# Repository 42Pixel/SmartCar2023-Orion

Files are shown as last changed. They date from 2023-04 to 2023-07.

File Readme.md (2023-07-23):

# 第十八届大学生智能汽车竞赛——猎户座

## 仓库简介
&emsp;&emsp;该仓库为第十八届大学生智能汽车竞赛安徽赛区**猎户座**参赛队伍项目仓库，保存了目前猎户座的全部软硬件资料。

## 目录结构
```
└─Fastest-Car
│  └─ProjectFiles
│      ├─Appendix
│      ├─Hardware
│      │  ├─无线串口模块
│      │  └─猎户座
│      │      ├─FastestCar-Motor
│      │      ├─FastestCar_Ctl
│      │      └─Library
│      └─Software
```
**[Appendix](https://github.com/42Pixel/Fastest-Car/tree/main/ProjectFiles/Appendix):** 附件文件夹，存放参考原理图，开源库，图片等相关文件

**[Hardware](https://github.com/42Pixel/Fastest-Car/tree/main/ProjectFiles/Hardware):** 硬件文件夹，存放相关硬件资料:

&emsp;&emsp;<font size=2>[无线串口模块](https://github.com/42Pixel/Fastest-Car/tree/main/ProjectFiles/Hardware/%E6%97%A0%E7%BA%BF%E4%B8%B2%E5%8F%A3%E6%A8%A1%E5%9D%97): 基于433MHZ模块设计的用于智能车急速越野组户外数据透传使用(该项目利用立创EDA设计，请使用立创EDA导入)</font>

&emsp;&emsp;<font size=2>[猎户座](https://github.com/42Pixel/Fastest-Car/tree/main/ProjectFiles/Hardware/%E7%8C%8E%E6%88%B7%E5%BA%A7):  根据开源项目：[逐飞科技基于英飞凌TC264 GTM单元的智能车BLDC开源项目](https://gitee.com/seekfree/TC264_GTM_BLDC_Project.git)修改而成。“[FastestCar-Motor](https://github.com/42Pixel/Fastest-Car/tree/main/ProjectFiles/Hardware/%E7%8C%8E%E6%88%B7%E5%BA%A7/FastestCar-Motor)”为无刷电机驱动部分，“[FastestCar_Ctl](https://github.com/42Pixel/Fastest-Car/tree/main/ProjectFiles/Hardware/%E7%8C%8E%E6%88%B7%E5%BA%A7/FastestCar_Ctl)”为驱动控制部分，“[Library](https://github.com/42Pixel/Fastest-Car/tree/main/ProjectFiles/Hardware/%E7%8C%8E%E6%88%B7%E5%BA%A7/Library)”为元器件封装库</font> 

**[Software](https://github.com/42Pixel/Fastest-Car/tree/main/ProjectFiles/Software):** 软件文件夹，存放程序固件。

## 相关图片

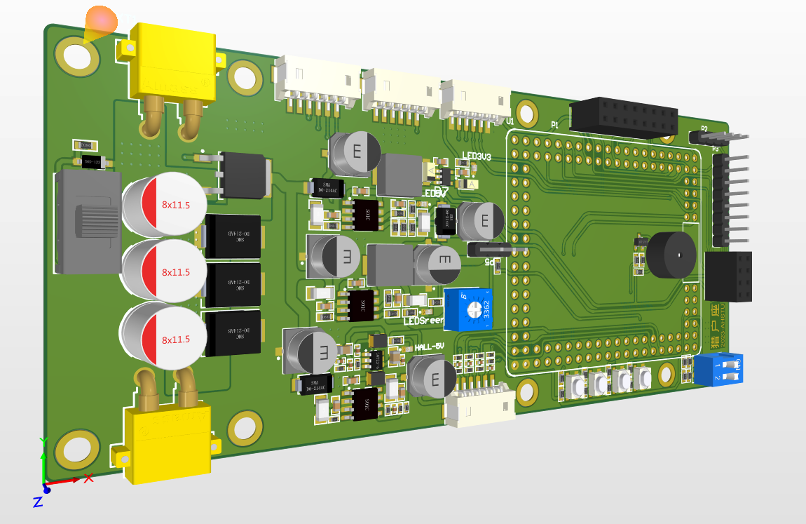
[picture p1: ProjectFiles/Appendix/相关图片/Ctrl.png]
母板

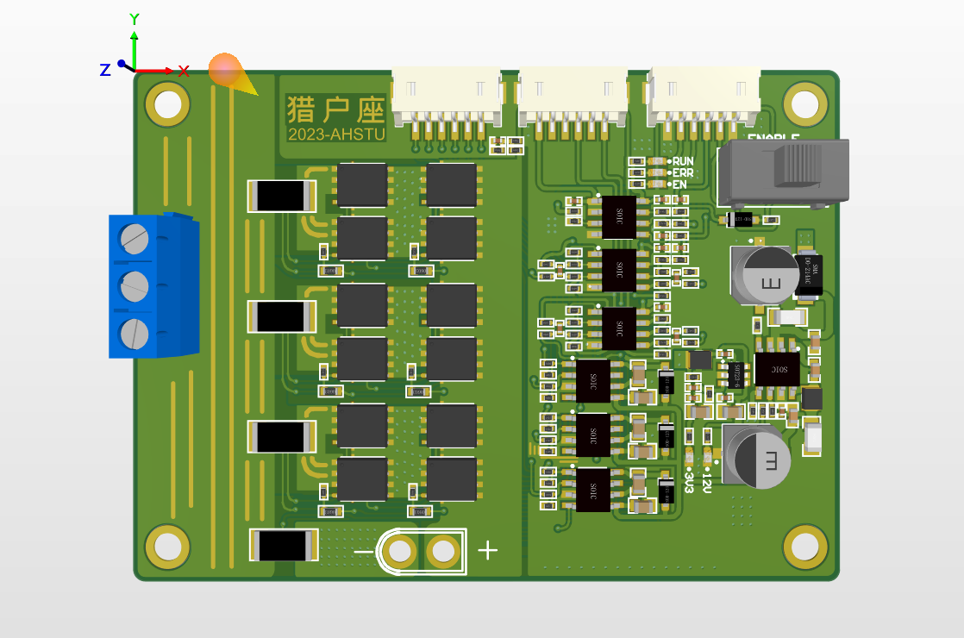
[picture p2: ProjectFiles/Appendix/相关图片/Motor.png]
电机驱动板

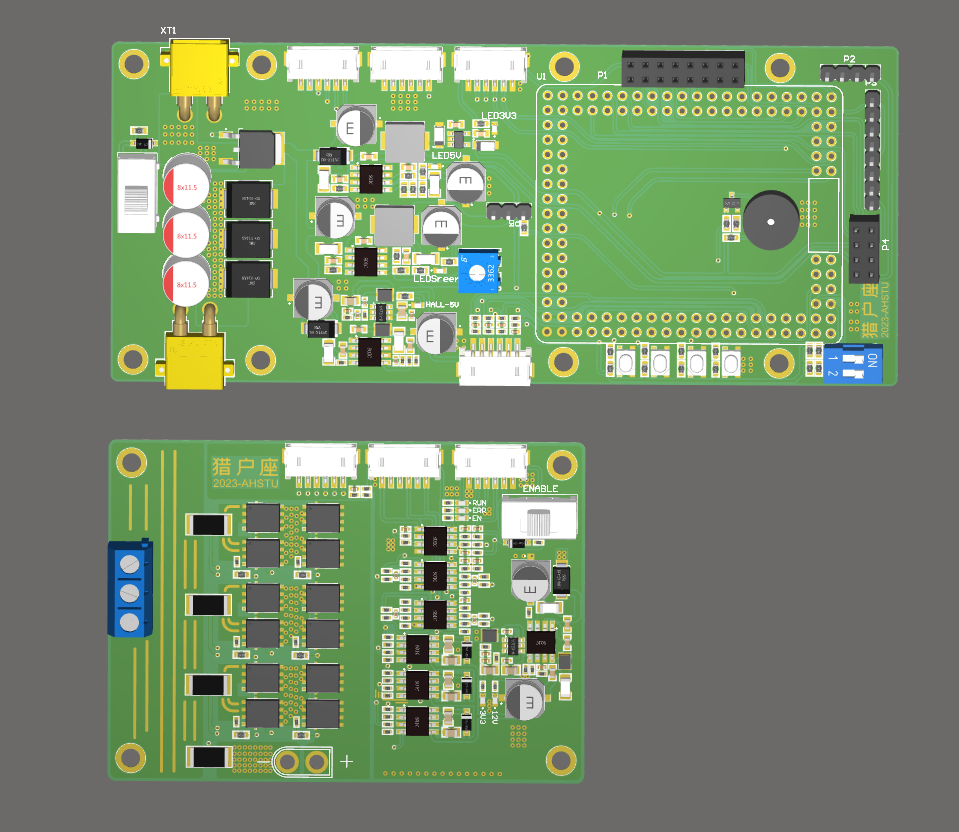
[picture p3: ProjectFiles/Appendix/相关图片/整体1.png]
整体

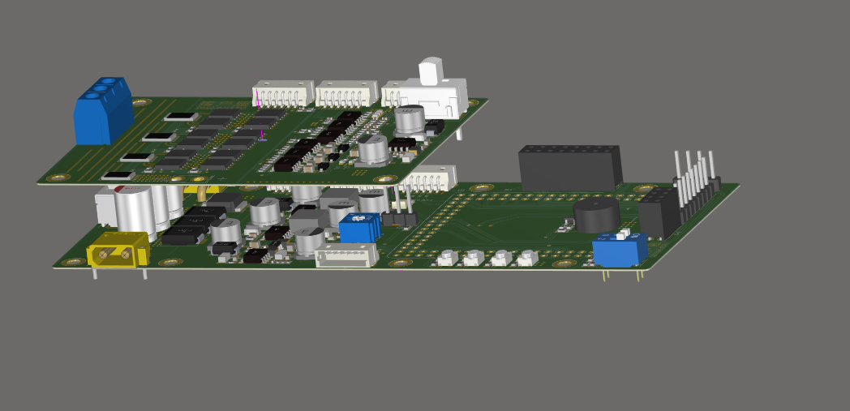
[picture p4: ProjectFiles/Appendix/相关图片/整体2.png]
组合


## 注意事项
:one: 由于本人代码水平有限，未能成功参赛，Sorftware文件夹中为未完成内容，无法直接用于参赛。

:two: 无线串口模块采用433MHZ透传模块，该模块并不支持一对一配对绑定，当有多个无线串口使用时会出现数据干扰。

:three: 无线串口模块采用嘉立创EDA设计导出，请使用嘉立创EDA导入打开。

:four: FastestCar-Motor项目中，采用双GND线路，即无刷电机与运放、预驱、状态反馈电路并不共地。在焊接调试时，请注意GND线路连接情况。

:five: FastestCar-Motor项目中，若12V-3V3电路无法输出3V3电压，请将RY8121的前馈电容移除。

## 参考资料
[第十八届全国大学生智能车竞赛竞速比赛规则](https://blog.csdn.net/zhuoqingjoking97298/article/details/127817742)

[遇到困难睡大觉-2022智能车工程](https://gitee.com/zhewana/TroubleSleeping_2022)

[(智能车比赛)基于 ADS 逐飞库 英飞凌 TC264 377系列 的多核使用经验](https://blog.csdn.net/zhou_zhuo/article/details/128751309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)

[第十七届智能车竞赛--极速越野组总结报告](https://blog.csdn.net/m0_46430715/article/details/126709805)

[MM32_CLion](https://github.com/ZhuYanzhen1/MM32_CLion)

[智能车视觉组仓库](https://github.com/0clock/smartcar2022)

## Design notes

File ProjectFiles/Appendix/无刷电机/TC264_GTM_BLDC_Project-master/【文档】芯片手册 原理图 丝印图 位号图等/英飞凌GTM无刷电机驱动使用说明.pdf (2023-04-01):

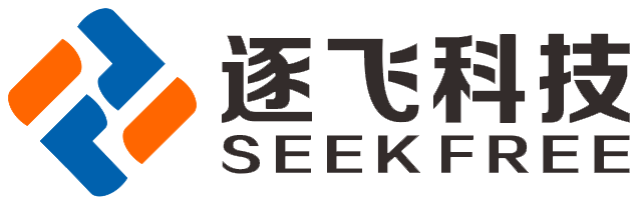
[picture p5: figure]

2021

# 英飞凌无刷电机驱动使用说明

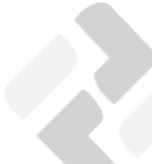
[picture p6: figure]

英飞凌无刷电机驱动使用说明 | 逐飞科技
目录

# 1.英飞凌无刷驱动正面接口介绍

## 1.1.正面接口图

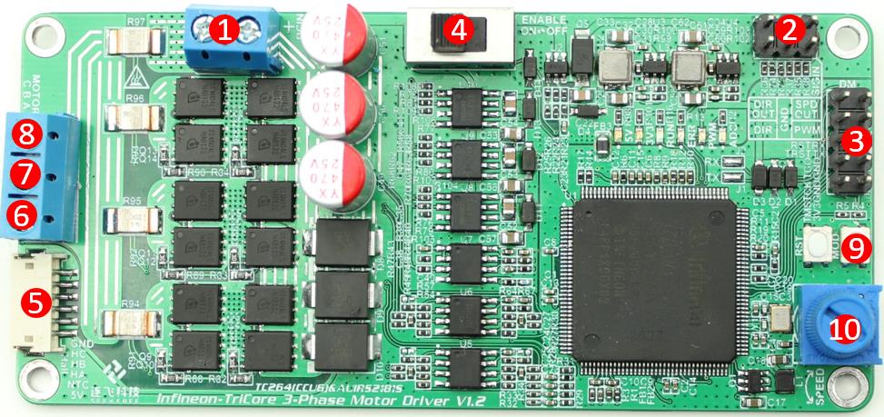
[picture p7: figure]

## 1.2.正面端口介绍

1：DCIN，直流电源接口，使用 12V 电源供电，建议使用 3S 电池。

2：控制输入与信息输出端口，PWM 引脚是速度调节端口，外部控制器输出 PWM，通过

调节占空比大小来调节速度。DIR 引脚是用于设置电机转动方向的；SPDOUT 与 DIROUT 引

脚是输出电机转速信息的，电机转得越快此引脚上输出的信号频率越高，推荐使用单片机采集

编码器的接口进行信息采集。SPDOUT 连接编码器采集接口的 A 通道或者连接单片机的计数

通道，DIROUT 连接编码器采集接口的 B 通道或者连接方向引脚（具体可以参考编码器采集例

程）。

3：调试接口，可以对电机驱动上的单片机烧写程序以及在线调试。

4：电机驱动的使能开关，开关是连接到 IO 上，通过单片机硬件实现的使能。

4：无刷电机接口，接入无刷电机的 A、B、C 三相。

5：无刷电机霍尔接口，连接无刷电机霍尔接口。

6：连接无刷电机 A 相。

7：连接无刷电机 B 相。

8：连接无刷电机 C 相。

7：电源 LED 灯，给驱动供电时此灯亮起。

9：板载按键，用来更改输入来源，在板载电位器和用户 PWM 输入之间切换，也可以自

己改成其他功能。

10：板载电位器，可通过板载电位器开环测试电机。

# 2.无刷电机接口介绍

## 2.1.无刷电机接口图片

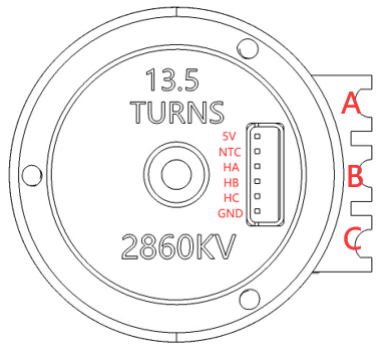
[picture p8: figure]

## 2.2.无刷电机接口介绍

无刷电机接口图片，如上图所示。

引脚 | 定义
5V | 霍尔传感器 5V 供电
NTC | 内部热敏电阻
HA | A 相霍尔线
HB | B 相霍尔线
HC | C 相霍尔线
GND | 接地
A、B、C | 三相电源线

# 3.驱动使用方法及硬件接线示意

## 3.1.使用方法

1：连接 12V 电源。

2：连接无刷电机霍尔线，连接无刷电机 A、B、C 三相电源线。

3：打开使能开关。

4：使用主控芯片给出 PWM 和 DIR 信号，电机开始运行。

## 3.2.硬件接线示意图

### 3.2.1.无刷电机与驱动接线示意图

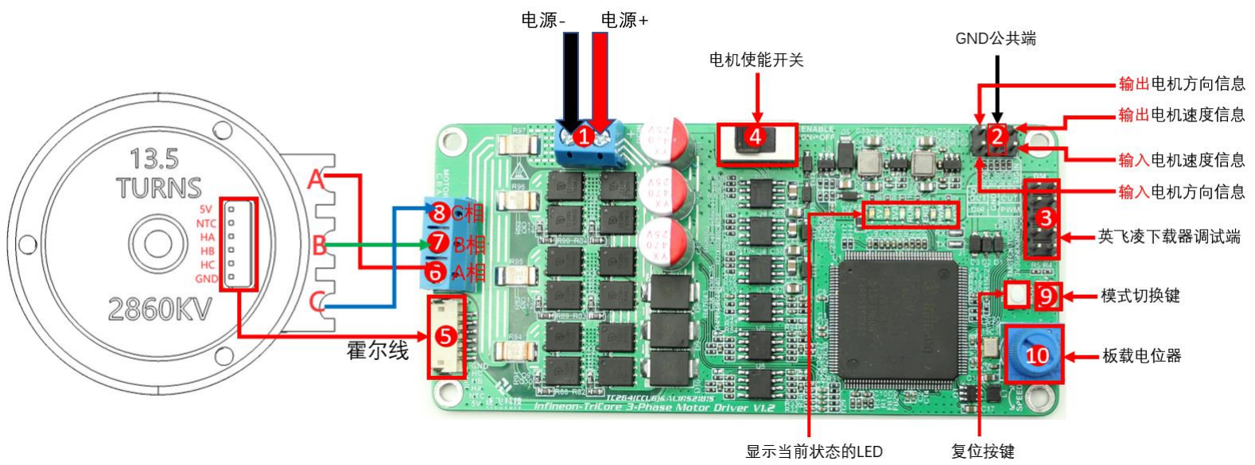
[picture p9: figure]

### 3.2.2.主板与驱动板接线示意图

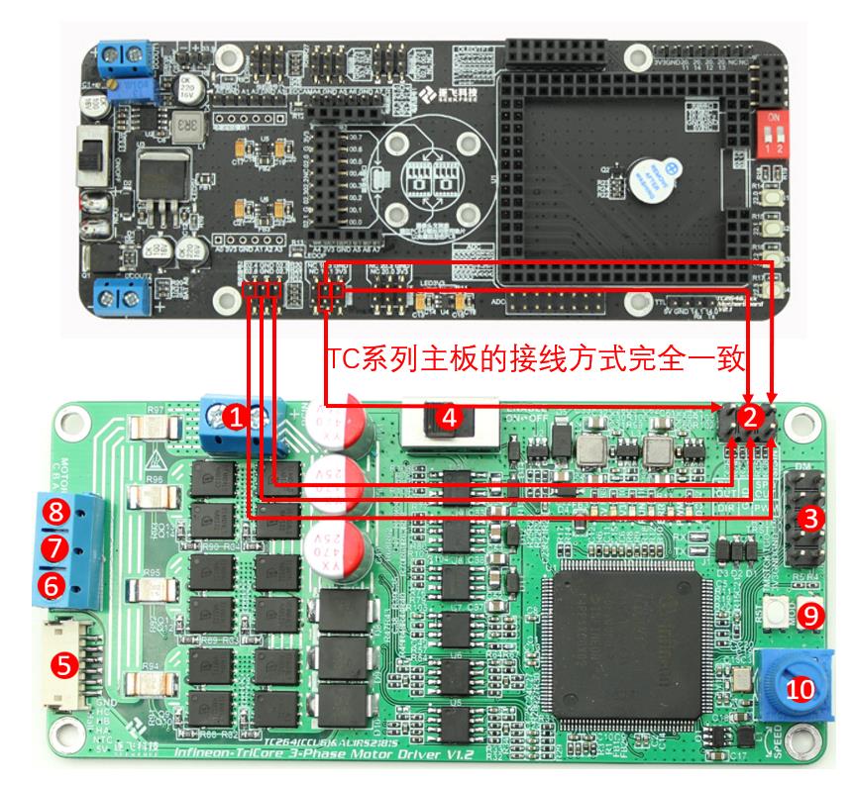
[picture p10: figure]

# 4.驱动使用方法及注意事项

## 4.1.简易测试方法

拿到无刷电机驱动时，如果需要测试驱动是否正常，可以按照上述 1、2、3 步骤操作完成

后，可以手动旋转无刷电机，如果使能灯亮起，则代表程序以及霍尔检测正常；之后可以将 3.3V

电源接到 PWM 口，查看电机是否旋转。注意：此时相当于让电机满占空比运行，电机转动非

常快，可以让 PWM 引脚接触一下高电平，电机运行后马上断开，此时电机会马上刹车停止。

## 4.2.注意事项

1、 | 无刷电机驱动内部已经下载过程序，可以直接使用，不建议拿到之后立马下载程序。
2、 | 测试电机前，检查不要有阻挡物导致电机堵转。
3、 | 连接电机线时，先连接霍尔线再连接三相电源线。
4、 | 测试无刷电机时，应将电机和驱动板应放置在绝缘物品上。
5、 | 测试无刷电机时，应该保证电机和驱动板能够及时散热。
6、 | 如果使用其他类型的无刷电机，请勿直接上电驱动。

# 5.运行参数

1：外部电源为 12V 供电，单片机为板载电源 5V 供电。

2：PWM 频率，建议使用 1KHz 的 PWM 进行驱动。PWM 频率过高可能会导致输入捕获

出错。

3：驱动可以通过虚拟示波器直接查看当前电机转速、当前霍尔位置、当前输入 PWM 占

空比等参数。

4：电机的死区大概为 2%的占空比。

5：当电源为 12V 时，电机的最高转速为每分钟 3W 转左右。

6：电机运行时，电流超过额定值(可以通过更改比较器电阻来修改额定值，具体电流值需

要通过计算得到)便会进入刹车模式(关闭定时器输出)。

# 6.驱动固件更新

购买的无刷驱动是下好固件的，我们后续可能会进行固件的升级维护，同学们需要自行下

载更新。同学们自己制作的灵动无刷电机驱动也可以使用我们的固件进行使用。

英飞凌无刷电机开源地址：

https://gitee.com/seekfree/TC264_BLDC_Project

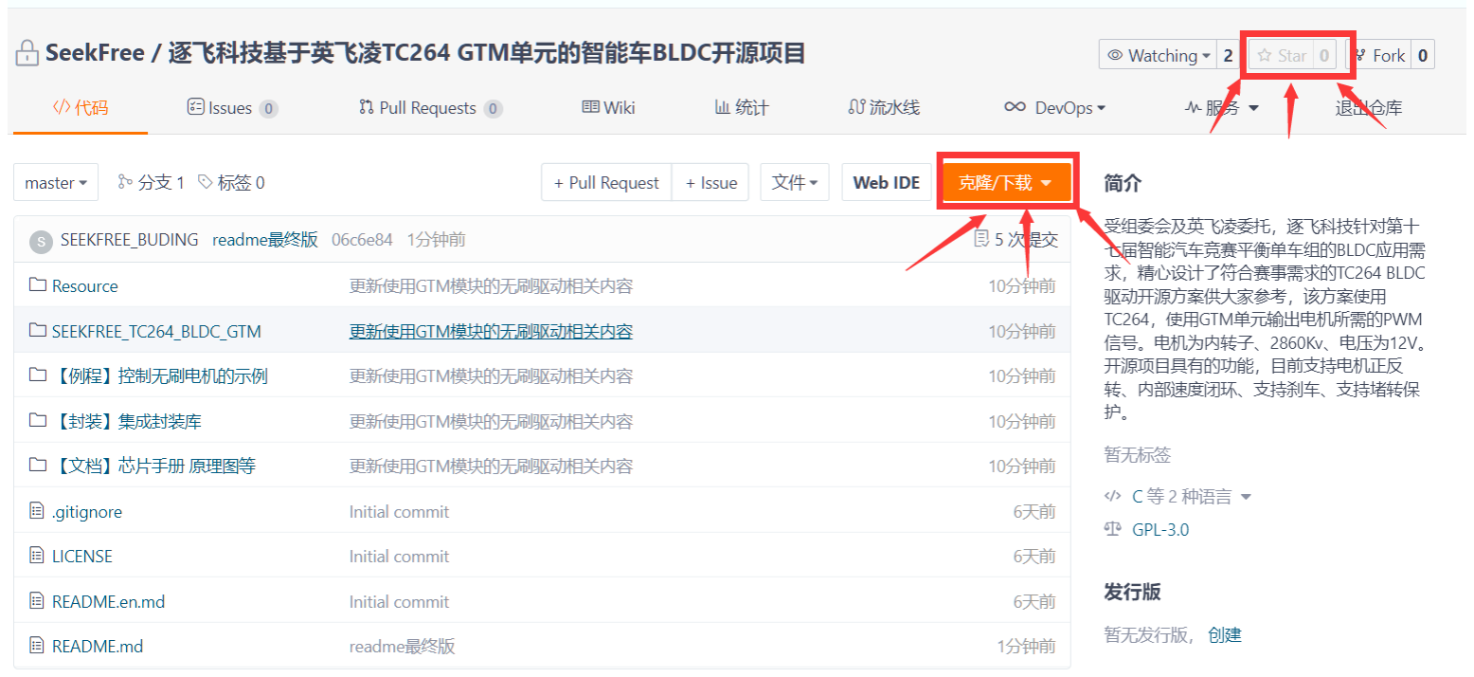
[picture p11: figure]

打开网页之后点击下载即可，各位同学下载之前别忘了帮我们点一点小星星哦，感谢同学

们的支持。

## 6.1.开源库各文档说明

Resource：存放本次开源所使用到的图片、视频等资源。

SEEKFREE_TC264_BLDC_GTM：无刷驱动的工程文件，可以通过此工程来更新固件，也可

以在阅读并理解了无刷电机原理之后来修改代码。

【封装】集成封装库：存放驱动板所使用到的元器件的 AD 集成封装库，同学们可以使用

此封装库进行原理图绘制。

【例程】控制无刷电机驱动的示例：存放使用 TC 系列主板控制无刷电机的例程，该程序

为主板例程。请勿下载到驱动板！请勿下载到驱动板！请勿下载到驱动板！请先参考主板与驱

动板连接示意图之后再进行程序烧录。

【文档】芯片手册 原理图等：存放无刷驱动原理图及使用说明等文件。

README.md：逐飞科技微信公众号发布的文档文件，可以通过阅读此文档初步了解无刷

电机原理，驱动板硬件原理图简述以及软件部分说明。

## 6.2.驱动固件更新方法

下载之后，将压缩包解压。打开文件夹“TC264_GTM_BLDC_Project-master”。

打开“SEEKFREE_TC264_BLDC_GTM”文件夹，此文件为驱动的代码工程。

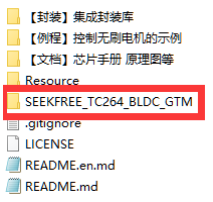
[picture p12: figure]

这个就是我们的工程文件了

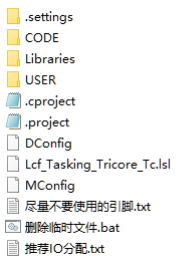
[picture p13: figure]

使用 AURIX Development Studio 添加此工程文件，编译结束后即可下载程序了。

# 7.文档版本

版本号 | 日期 | 内容变更
V1.0 | 2022-04-21 | 初始版本。

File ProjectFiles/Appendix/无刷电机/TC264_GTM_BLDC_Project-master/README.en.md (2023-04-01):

# 逐飞科技基于英飞凌TC264 GTM单元的智能车BLDC开源项目

#### Description
受组委会及英飞凌委托，逐飞科技针对第十七届智能汽车竞赛平衡单车组的BLDC应用需求，精心设计了符合赛事需求的TC264 BLDC驱动开源方案供大家参考，该方案使用TC264，使用GTM单元输出电机所需的PWM信号。电机为内转子、2860Kv、电压为12V。开源项目具有的功能，目前支持电机正反转、内部速度闭环、支持刹车、支持堵转保护。

#### Software Architecture
Software architecture description

#### Installation

1.  xxxx
2.  xxxx
3.  xxxx

#### Instructions

1.  xxxx
2.  xxxx
3.  xxxx

#### Contribution

1.  Fork the repository
2.  Create Feat_xxx branch
3.  Commit your code
4.  Create Pull Request

#### Gitee Feature

1.  You can use Readme\_XXX.md to support different languages, such as Readme\_en.md, Readme\_zh.md
2.  Gitee blog [blog.gitee.com](https://blog.gitee.com)
3.  Explore open source project [https://gitee.com/explore](https://gitee.com/explore)
4.  The most valuable open source project [GVP](https://gitee.com/gvp)
5.  The manual of Gitee [https://gitee.com/help](https://gitee.com/help)
6.  The most popular members  [https://gitee.com/gitee-stars/](https://gitee.com/gitee-stars/)

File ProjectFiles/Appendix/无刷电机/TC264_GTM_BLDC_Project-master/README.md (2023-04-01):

# 基于英飞凌MCU GTM模块的无刷电机驱动方案开源啦

#### 介绍
各参赛同学好，关注了逐飞科技微信公众号的同学应该还记得，受英飞凌委托，逐飞科技在2021年12月9日发布了针对第十七届无刷电机驱动的开源项目，供大家参考，相信已经有部分同学根据之前的开源方案玩起来了，还没注意到原开源项目的可以通过此篇推文进行了解，“英飞凌BLDC驱动方案开源啦--逐飞科技”可以和今天的方案进行对比穿插学习，以便达到更好的理解效果。

 在上一个项目开源后，我们又了解到不少同学都想把无刷驱动和主板合二为一，使用一颗TC264芯片来控制所有的外设，但是前段时间开源的无刷驱动项目使用的是CCU6模块，需要CPU频繁的处理无刷驱动的换相控制，所以不少同学就担心后期CPU可能会处理不过来，同时英飞凌也希望我们再制作一个基于AURIX系列MCU GTM模块的无刷驱动方案供同学们参考，于是一拍即合，今天给同学们带来了一个新的无刷驱动开源方案——基于Infineon MCU GTM的模块无刷驱动开源方案。

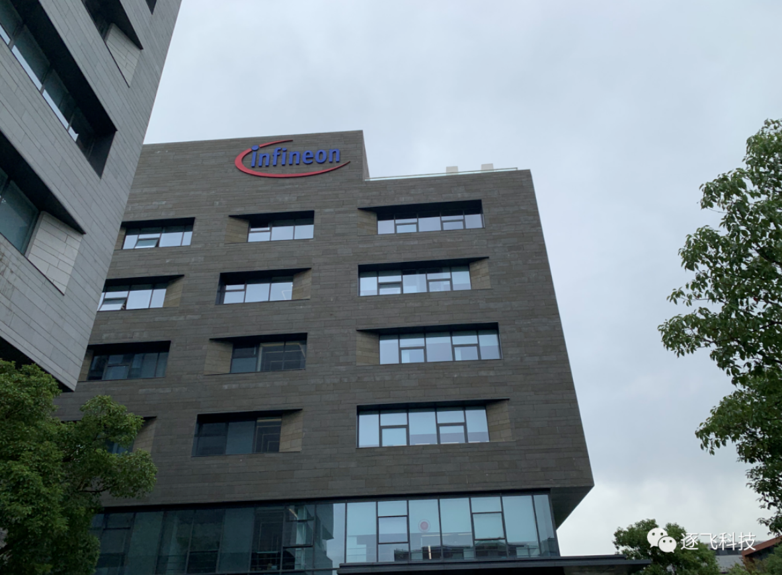
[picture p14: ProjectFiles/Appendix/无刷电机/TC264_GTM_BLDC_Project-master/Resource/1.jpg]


#### 一、无刷电机原理
自第十七届智能汽车竞赛规则发布以来，这已经是逐飞发布的第三个关于无刷驱动的开源项目了，相信参加允许使用无刷电机组别的大部分同学都已经对无刷电机的旋转原理比较熟悉啦，不过为了方便阅读，请大家允许我们在这里再简要的讲解一下无刷电机的原理部分。

#### 1.1.无刷电机内部结构

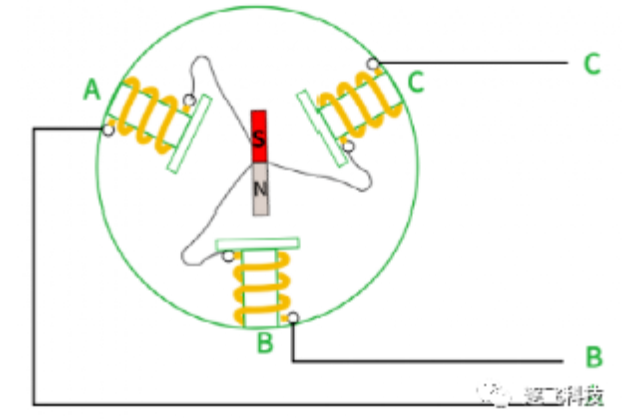
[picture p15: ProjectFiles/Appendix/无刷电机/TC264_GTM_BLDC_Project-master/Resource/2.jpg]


上图为无刷电机内部导线连接情况的简笔画，可以看到有三个线圈，每个线圈的一端都连接起来，另外一端引出到外部，在无刷电机的结构中我们一般称线圈的部分为定子。而中间部分则有一个具有N/S两极的永磁铁，我们一般称它为转子。大家有没有发现无刷电机中的定子和转子跟有刷电机的定子和转子的定义是不是恰恰相反呢？

#### 1.2.无刷电机旋转原理

根据无刷电机内部结构我们发现无刷电机的引出来的线有三根，而我们的电源线只有两根，那么这个时候我们将无刷电机的任意两根线与电源线连接会发生什么呢？大家看下图：

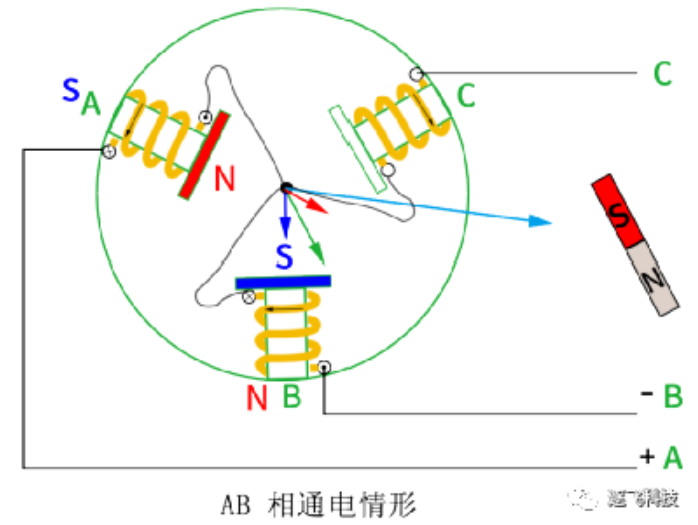
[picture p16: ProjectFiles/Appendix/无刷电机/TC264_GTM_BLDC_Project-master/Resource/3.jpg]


我们将电源正极接到了A相，电源负极接到了B相，此时由于无刷电机内部是一个个由相线围绕而成的线圈，那么就我们给相线通电就相对于给线圈通电了，而给线圈通电就会产生什么？没错，就是磁场！

既然产生了磁场，那么就肯定会有磁极，磁极方向的判断我们在初中阶段就有略微了解，对于这种通电线圈的磁极判断就需要用到“右手螺旋定则”，根据右手螺旋定则我们可以很轻松的判断出上图中通电线圈产生的磁场的极性：A线圈产生N极朝里S极朝外的磁场，B线圈产生S极朝里N极朝外的磁场。

而根据无刷电机的结构图我们知道无刷电机内部是有一个永磁铁作为转子的，那么此时围绕定子的线圈产生了磁场，就会迫使永磁转子改变当前的位置。我们都知道“同极相斥，异极相吸”，根据这个我们就可以判断出永磁定子被迫改变的位置如何，其实就和上面的图一致。

上面的图是电源正极接到了A相，电源负极接到了B相，我们已经分析了内部转子被迫改变位置的情况，那么如果我们反过来接呢？把电源正极接到B相，电源负极接到A相，就像下面的图一样，这个时候大家猜猜会发生什么？

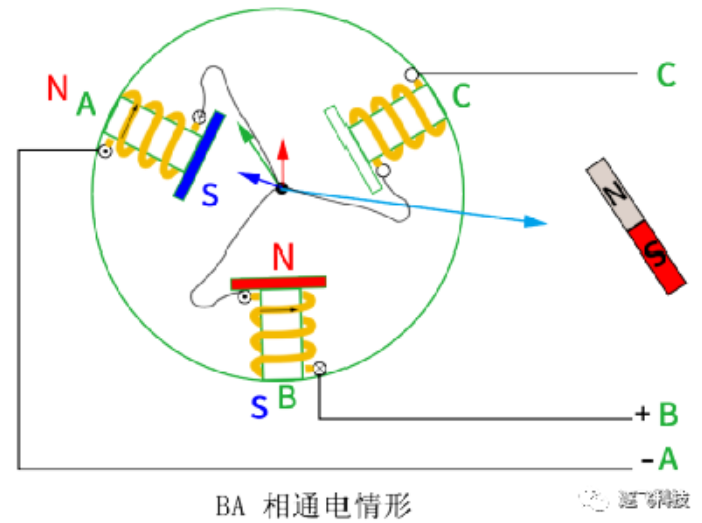
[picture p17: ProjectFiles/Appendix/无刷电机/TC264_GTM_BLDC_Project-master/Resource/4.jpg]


对的，所有的极性相对于A正B负的时候完全交换过来了，转子也完全旋转了180°，具体的极性大家可以用右手螺旋准则判断一下，这里就不再细讲啦。

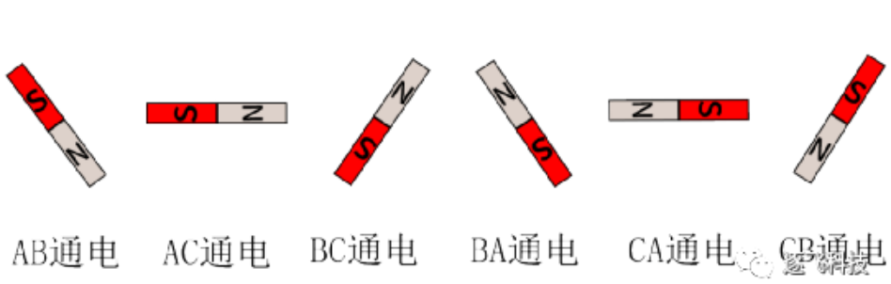
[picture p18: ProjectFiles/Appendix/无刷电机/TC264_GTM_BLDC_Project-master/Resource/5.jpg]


我们现在是给无刷电机的两根线通电的情况，但是无刷电机有三根线，那么我们两两通电的组合就有三种，再区分电流方向的话就有6种，那么这6种不同情况下转子的位置就和上图一样啦。

从左到右顺着排序的话，可以看出来相邻转子的角度都互差了60°，那么如果我们能使用程序来控制，按照顺序切换相线的通电情况，那么转子是不是就转起来了呢？结果也确实是这样的，但是还少了一个比较关键的东西，那就是我们应该如何检测到转子的当前角度。如果对原理还有不明白的，可以通过文章开头的超链接进入去年12月9号发布的推文，那篇文章更详细的讲解了设计原理。

#### 1.3.霍尔位置检测

无刷电机其实分为有感无刷和无感无刷，这里的有感和无感就是有没有传感器来感知转子角度的意思，但是无论是有感无刷电机还是无感无刷电机，我们都需要通过各种方法来获得转子的角度。

这里主要给大家讲的是有感无刷电机中的霍尔检测方法。

通过安装霍尔来检测转子位置，一共安装三个霍尔分别间隔120度安装，霍尔输出的波形如下图所示(使用逻辑分析仪采集到的波形)，当电机的转子位置改变的时候，就会影响霍尔元件的开关状态，从而输出高低电平。

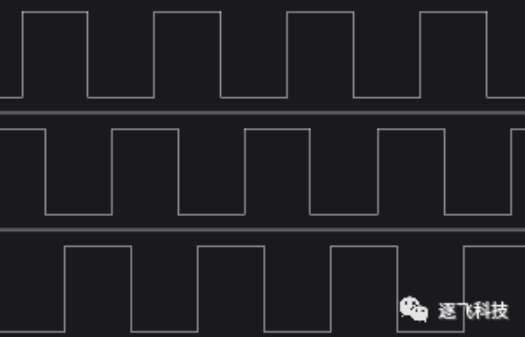
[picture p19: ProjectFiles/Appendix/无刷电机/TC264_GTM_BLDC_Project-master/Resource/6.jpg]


心细的同学应该已经发现了三个霍尔的组合状态恰好是6种，而我们上面分析的通电情况也是6种，那么这两个之前是不是有对应关系呢？没错，它们就是对应的，霍尔元件是呈120度摆放的，那么霍尔的6种状态的切换间隔也是60°，恰好就与固定两相通电的转子角度对应了。

所以这个时候就可以梳理出大致的无刷电机控制原理了：

1.通过霍尔传感器检测当前转子所在的角度区间

2.通过判断当前转子角度区间来让单片机输出下一个区间的控制信号

3.控制信号通过预驱和MOS开关输出到电机

4.当转子到达下一个角度区间时，重复第一步

同样，如果对这部分也比较生疏的还是推荐去年12月9号发布的推文，里面有详细讲解。

#### 二、GTM模块介绍

#### 2.1.GTM模块简述

GTM(Generic Timer Module)，直译出来就是通用定时器模块的意思，但是它又与我们平时理解的通用定时器有点不同，我们平时用定时器无非就是用来输出PWM信号或者用于周期中断等等，这些功能GTM模块都支持，而且还有一些我们没了解过的功能，大家看下图：

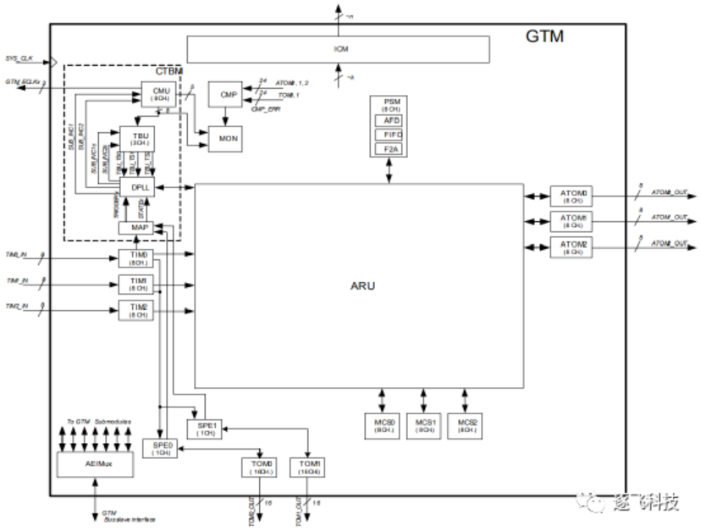
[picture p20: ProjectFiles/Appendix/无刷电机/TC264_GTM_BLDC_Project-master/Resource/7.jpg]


这个就是GTM模块的总体框图啦，我们第一眼肯定看到的就是里面最大的模块-ARU模块，它是用来处理数据流的，并且可以控制整个GTM模块的输出，但是它不是我们今天的主角，我们的主角在ARU模块的左侧和左下部分，分别是TIM模块、SPE模块、TOM模块，这几个模块的组合实现了单片机硬件检测霍尔并且换相输出的操作，我们的CPU就不用再反复执行无刷电机驱动部分的代码了。

#### 2.2.驱动逻辑分析

在单独介绍我们要用到的这几个模块之前，我们先简单描述一下它们的工作流程。

TIM模块负责采集霍尔信号并且对其进行滤波，然后将霍尔信号送到SPE模块，SPE模块通过判断当前的霍尔值来控制TOM模块输出固定相位的PWM信号，而这个固定的相位就是我们初始化时预先在SPE模块中写好的一个换相表。具体的工作流程大家可以看看下图：

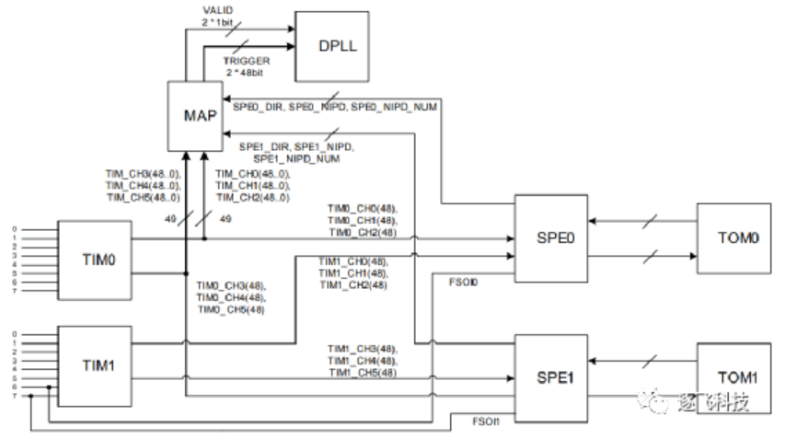
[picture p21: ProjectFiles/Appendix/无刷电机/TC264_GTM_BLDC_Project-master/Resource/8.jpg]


#### 2.2.1.TIM模块

TIM（Timer Input Module）模块，定时器输入模块。

在我们的实际应用中，该模块主要负责采集霍尔信号和刹车信号，同时模块自带滤波功能，保证捕获到的是准确的值。TIM模块会将捕获到的霍尔值直接送到SPE模块进行后续处理。

从上面总的工作流程图可以看出来TIM0模块的输入有8个通道，而我们只用了三个用于捕获霍尔信号，然后将处理好的三路霍尔信号送到了SPE0模块。

#### 2.2.2.SPE模块

SPE (Sensor Pattern Evaluation) 模块，传感器评估模块。

SPE模块专用于评估当前霍尔信号的值，并且根据当前的霍尔值去查表通过寄存器控制TOM模块的输出，具体控制逻辑看下图：

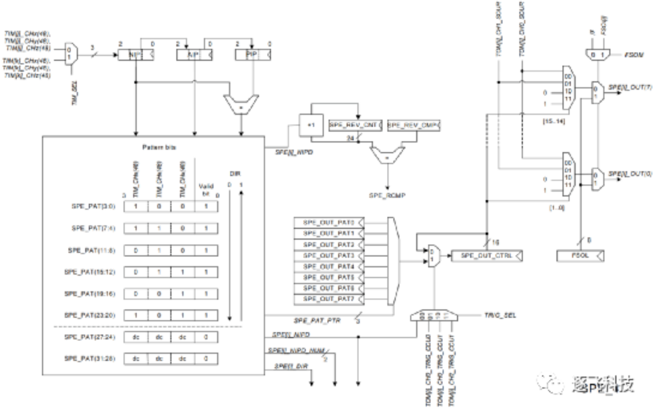
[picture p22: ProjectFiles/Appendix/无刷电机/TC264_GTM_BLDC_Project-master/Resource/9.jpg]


左上角的三路信号就是由TIM模块滤波之后送过来的信号，然后通过NIP寄存器进行保存（我们通过读取NIP寄存器就可以知道当前的霍尔值），之后三路信号分别送到了Pattern进行查表，这里的查表是查的霍尔与输出的对应关系，比如霍尔实际值是1，然后查表输出值是3，那么后面就会根据查表输出的霍尔值来再次查表输出实际PWM的控制值。上图中，SPE_PAT_PTR就是根据实际霍尔值查表输出的矫正值，而SPE_OUT_PATx是控制PWM输出的寄存器值，将SPE_OUT_PATx的值根据SPE_PAT_PTR送到SPE_OUT_CTRL寄存器，后续的输出就是判断SPE_OUT_CTRL寄存器的内容来控制不同端口的输出情况。

值得注意的是，右上角的刹车信号是通过FSOI进行控制，当FSOI为有效时，最终的输出将被修改为FSOM寄存器的输出值，而FSOM寄存器的是我们在初始化时就给了的，我们只要设置FSOM寄存器是控制所有上桥关闭、所有下桥开启，那么就是正常的刹车效果。

#### 2.2.3.TOM模块

TOM（Timer Output Module）模块，定时器输出模块。

该模块将根据设置的参数生成PWM信号，以及根据SPE模块选择的输出通道输出PWM信号或者是高低电平，从而驱动无刷电机旋转。

#### 三、硬件原理图分析

关于驱动电路的预驱动及MOS选型在之前的推文中已经讲过，这里就不再重复了，下面主要讲一下原理图中值得注意的地方，图看不清不要紧，后续会将原理图开源放到Gitee，大家可以去自行下载。

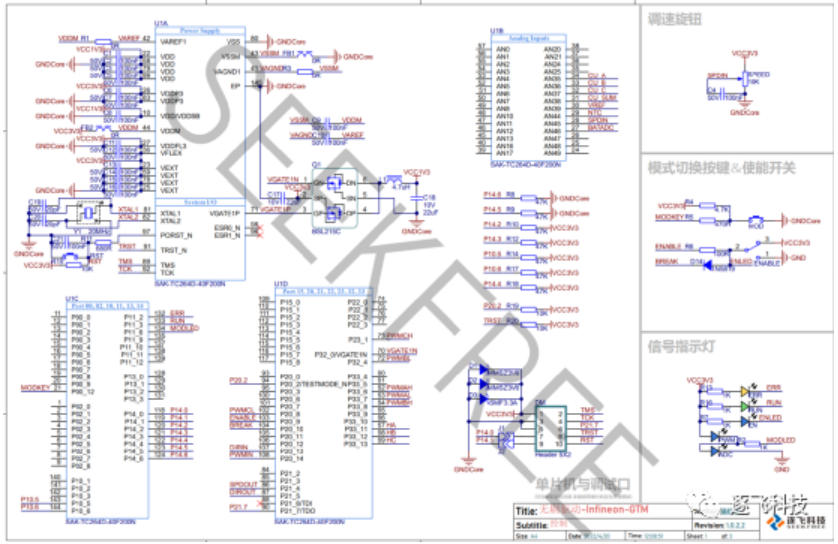
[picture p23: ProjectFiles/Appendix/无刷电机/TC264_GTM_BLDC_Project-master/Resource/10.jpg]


这个是TC264核心的部分外围电路，相较于之前开源的CCU6方案并未作太大改变，仅把控制输出端口、霍尔输入端口、输入捕获端等端口稍微做了修改，想要做一体板的同学也不用担心新的端口和原来的主板端口会有太多冲突，我们GTM模块所使用的引脚仅和一个编码器的端口稍有冲突，其他的完全和主板的端口避开的，所以大家完全可以放开手去做啦~

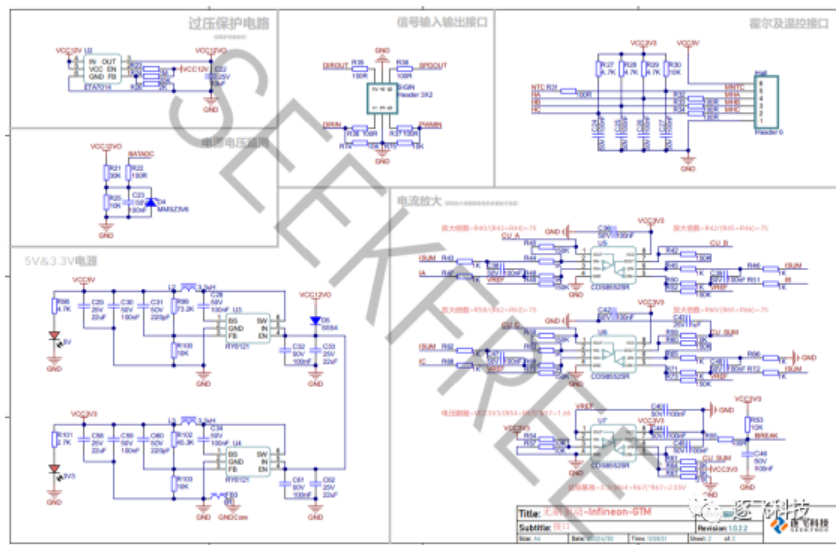
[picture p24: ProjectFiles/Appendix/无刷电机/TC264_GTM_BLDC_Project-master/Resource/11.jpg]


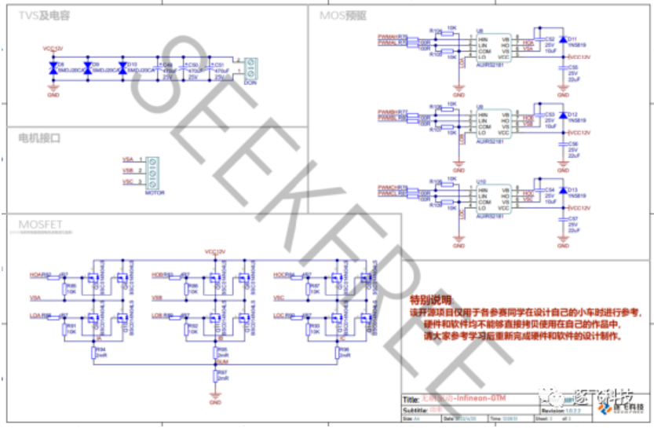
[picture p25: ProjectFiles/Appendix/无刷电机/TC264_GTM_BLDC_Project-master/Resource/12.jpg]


后面的电源部分、电流采集部分、预驱和MOS开关部分则是与之前的CCU6方案完全一致。所以预驱和MOS的芯片选型这里就不再赘述啦。

#### 四、程序运行流程

#### 4.1.GTM模块无刷驱动开源项目的代码部分

#### 4.1.1.开源项目的工程目录结构

逐飞Infineon智能车BLDC开源项目的目录结构如下图所示。
 
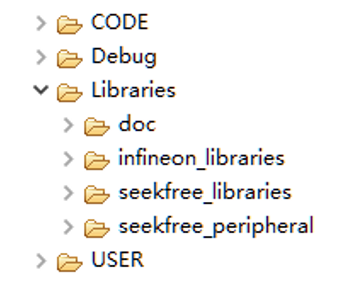
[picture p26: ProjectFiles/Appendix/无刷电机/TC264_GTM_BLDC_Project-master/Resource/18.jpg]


CODE文件夹下放置的是逐飞科技精心编写的无刷电机驱动相关代码。 Infineon_libraries是英飞凌官方的底层驱动，如果还需要其他的单片机片内外设功能，可以基于Infineon_libraries自行编写程序实现。 Seekfree_libraries和seekfree_peripheral则是逐飞基于TC264制作的应用底层库。 user文件夹下放置的是主程序及中断文件。

#### 4.1.2.无刷电机驱动需要用到的相关内外设以及驱动代码
 
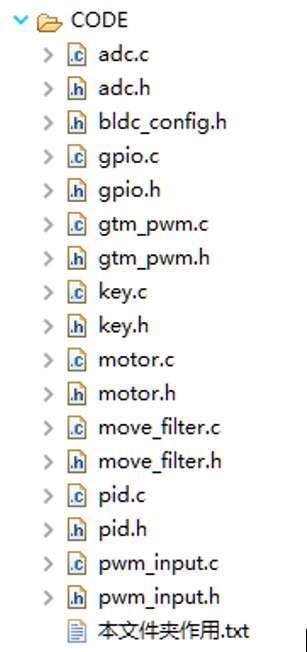
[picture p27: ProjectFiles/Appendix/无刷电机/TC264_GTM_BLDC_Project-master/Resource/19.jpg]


无刷电机需要用到的单片机片内外设有： 
ADC：主要用于检测电源电压、采集放大时候的母线电流以及相电流 
GTM定时器：主要用于输出电机所需要用到的互补PWM信号，并且实现自动堵转保护，无需代码干预，当母线 电流超过设定值的时候，自动关闭定时器输出。
GPIO：主要用于LED指示灯，用于显示各种状态，并且初始化输出方向信息和速度信息的端口。 
按键：通过板载的按键来改变输入来源，可在板载电位器和用户PWM信号之间切换。
PWM输入：使用GTM模块的输入捕获实现对外部PWM信号的周期以及占空比获取。

无刷电机的驱动文件有： bldc_config.h文件用于配置电机参数，例如是否开启闭环、是否开启刹车、最大转速设置。 hall文件主要用于检测霍尔的值、换相时间计算、转速计算。 motor文件主要用于电机占空比输出、速度计算、速度和方向信息输出。 move_filter文件主要用于，对数据进行滑动平均滤波。 pid文件主要用于对转速进行速度PID闭环。

#### 4.1.3.主函数及中断函数说明

主函数与中断的文件存放在USER文件夹中，无刷电机控制部分由GTM模块硬件完成，所以并没有代码用于控制无刷电机，中断相关的函数全部放在了isr.c中。

#### 4.1.4.GTM模块无刷·驱动开源项目的程序工作流程讲解

为了更清楚的表达起工作流程，整个项目的软件流程绘制了几张流程图，同时也加以文字说明。由于主要使用的GTM模块，所以程序部分就相对比较简单了。

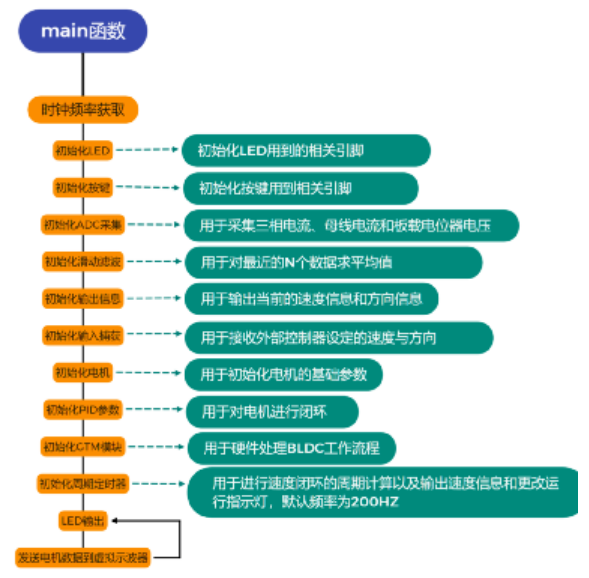
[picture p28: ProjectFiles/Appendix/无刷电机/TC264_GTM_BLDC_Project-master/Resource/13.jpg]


上图为本次开源驱动程序的主函数部分，不难看出来，处理初始化了几个无刷驱动固定的外设之后，就是GTM模块的初始化，我们在这里就把要硬件换相所使用到的TIM0模块、SPE0模块、TOM0模块都初始化一遍，初始化结束之后就已经实现硬件换相了，但是需要一个东西，那就是输出控制电机转速的占空比信息，因此最后我们还有一个固定的周期中断初始化。

输入图片说明

在定时器周期中断的服务函数中，我们进行了一些基础的按键扫描、电机旋转方向设置等跟无刷电机相关的基础操作，然后就是进行PID闭环运算，最后就是输出占空比了，只有输出带有效占空比的PWM信号才能让无刷电机转起来。

上面基本上已经完成了无刷驱动程序的全套内容，但是还差一个，那就是输入捕获，当然了，如果是制作一体板的同学就可以不需要这部分的内容。

输入图片说明

在分享CCU6方案时，我们就有用到输入捕获来捕获用户输入的PWM占空比信息，方便用户通过主板直接控制无刷电机旋转。同时，我们也有说到Infineon的输入捕获部分非常简单方便，仅需判断一下数据状态就可以得到捕获的占空比信息，其余的操作都已经在触发捕获中断之前完成了。

最后，当然是上开源项目gitee链接：

       https://gitee.com/seekfree/TC264_GTM_BLDC_Project

打包下载开源库压缩包，就可以愉快的开始玩无刷啦，各位下载之前别忘了帮我们点一点小星星哦，感谢各位的支持。

#### 五、结束语

为了测试方便，本开源项目的硬件依然是将TC264和驱动电路做在一个板子上的，同学们自己在做板子时可以考虑直接使用主控TC264来控制驱动输出，我们在引脚分配的时候也已经避开了常用的资源，也就是一颗TC264就既是小车的主控，也是无刷电机驱动的控制器，并且文章开头也说过，使用GTM模块来实现无刷驱动的方案也降低了CPU消耗，同时我们测试的板子是为了兼容更大的电流采用了MOS管并联，所以大家也可以根据实际需要来进行减半的设计，这样差不多就可以做到将驱动板缩小一半，并且也推荐大家用一颗TC264实现无刷驱动和主控两个需求，以适应平衡单车组的轻量化整体设计。所以本开源项目所对应的驱动板实物并未生产学习板来进行销售，目前逐飞在售的无刷驱动学习板只有CCU6的那种方案，所以同学们直接根据开源项目的原理图自行设计就行了。

无刷电机可以采用逐飞演示车模中推荐的型号，在越野组的开源方案中我们讲到过，我们对很多款电机进行了测试，单车平衡组最终采用的是和极速越野组的同一款电机，此款无刷电机力量和速度兼具，现货发售中，逐飞的开源项目代码和硬件也是以这款电机为样品来进行测试的。

这款电机的参数如下：有感、三槽两极、2860Kv（Kv表示每增加一伏电压电机增加的转速，最高12V）、尺寸36(mm)*50(mm)、额定功率190W、支持1-3S锂电池供电。

输入图片说明

温馨提示：此款电机仅为逐飞推荐款，同学们也可以选择自己认为合适的无刷电机，这一点上规则是没有限制的，但建议大家选择有感无刷。

以上开源项目经过逐飞的精心设计和代码编写，真实可靠，在昨天的直播中也进行了讲解，可以通过逐飞B站回看视频，平衡单车组的逐飞演示车模也是用的这套开源方案制作的，证明了此开源方案的可行性，剩下的就是大家尽情发挥自己算法的时候了。学习过程中可以结合直播视频回放和往期相关推文来加深理解，链接及直播回放链接见下方：

逐飞基于英飞凌MCU CCU6的无刷电机驱动方案开源项目：英飞凌BLDC驱动方案开源啦--逐飞科技

第十七届智能车竞赛英飞凌|逐飞联合专题培训之无刷电机驱动：
       https://www.bilibili.com/video/BV1JY411p7bH?spm_id_from=333.999.0.0

第十七届智能车竞赛英飞凌|逐飞联合专题培训之平衡单车入门讲解：
       https://www.bilibili.com/video/BV1er4y1H7Wt?spm_id_from=333.999.0.0

在英飞凌无刷驱动开源项目的研发过程中，英飞凌主任工程师Cobb老师给我们提供了很多技术支持和帮助，感谢英飞凌，感谢Cobb老师，期待能与英飞凌开展更深入的合作，获得更多的学习机会。更要感谢英飞凌为智能车竞赛提供的大力支持。

输入图片说明

好了，本期的开源项目介绍就到这里了，推荐款无刷电机、刷驱动学习板及平衡单车组学习套件均已上架逐飞淘宝店预售，感谢各位支持（seekfree.taobao.com），你们的支持是我们开源的动力，如果能帮到大家，深感荣幸。时间紧张，水平有限，大神轻拍，如果开源项目中有任何BUG，欢迎留言反馈，逐飞会持续维护和完善，也可通过QQ群与我们进行交流讨论（英飞凌平衡单车组技术支持交流群--逐飞科技：300610841）。欢迎各位持续关注“逐飞科技”微信公众号，逐飞的开源项目、技术分享及智能车竞赛的相关信息更新都会在该公众号上发布，点击下方通道即可关注。

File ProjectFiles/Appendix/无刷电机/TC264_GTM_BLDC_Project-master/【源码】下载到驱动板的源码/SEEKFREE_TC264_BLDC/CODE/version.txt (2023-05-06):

V1.0.1  增加科宇K1车模专用无刷电机驱动方式，通过更改bldc_config.h文件内的宏定义即可切换电机

V1.0.0  初始版本

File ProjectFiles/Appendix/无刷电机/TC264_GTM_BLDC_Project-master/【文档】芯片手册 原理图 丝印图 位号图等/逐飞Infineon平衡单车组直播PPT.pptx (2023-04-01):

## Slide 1


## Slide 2

目录

Contents

第一章

无刷电机原理

第二章

硬件部分

第三章

软件部分

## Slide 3

无刷电机原理


第一章

1

电机结构

2

旋转原理

3

霍尔结构

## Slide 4

1

电机结构

有刷电机结构：

无刷电机结构：


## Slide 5

2

旋转原理


结构简化图：


三个线圈进行星形连接


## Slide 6

2

旋转原理


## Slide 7

2

旋转原理


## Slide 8

3

霍尔结构

010

110

100

101

001

011


2

6

4

5

1

3

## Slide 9

第二章

硬件部分

1

芯片选型

2

MOS选型

3

原理图

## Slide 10

1

芯片选型

- 使用双核TriCore™架构的高性能 32 位微控制器。
- 芯片单核主频高达 200MHz。
- 容量高至2.5MB的ROM以及高至240KB的RAM，并且都带ECC（纠错编码）
- 包含4个12位SAR ADC转换器模块。
- 拥有CCU6高级定时器，可用于输出无刷电机所需要的控制信号，支持trap信号输入,用于实现快速关闭定时器输出。
- 拥有GTM高级定时器，支持输入捕获、PWM输出等功能，可用于输出无刷电机所需要的控制信号，支持快速关断功能。并且能同步捕获霍尔信号以及外部输入的PWM信号。
- UART 接口4 个、SPI 接口4 个。


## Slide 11

2

预驱及MOS选型

预驱：AUIRS2181

MOS：BSC014N04LS

- 最大电流198A
- 10V时，内阻仅1.4mΩ
- 开启电压非常低

- 驱动能力强，输出1.9A输入2.3A
- 支持电压10~20V，带有欠压保护
- 兼容3.3V和5V输入逻辑

详情链接：https://www.infineon-autoeco.com/BBS/Detail/63391

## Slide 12

3

电路原理图


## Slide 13

3

电路原理图


V

Vref

0

t

满足: (R43+R44)/(R40)= (R47+R48)/(R49)
CU_A=(R40)/(R43+R44) * (IA-ISUM) +VREF
CU_A=75 * (IA-ISUM) +VREF
假设单片机12位采集值为：2400
那么电流计算如下：
IA=(2400−2048)/4096 ∗3.3 ÷75÷0.002≈1.89A

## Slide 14

3

电路原理图


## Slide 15

1

编译环境介绍

第三章

2

工程目录结构

软件部分

3

资源使用讲解

4

程序运行流程

5

实际效果演示

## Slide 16

1

编译环境介绍

AURIX Development Studio V1.5.2

下载链接：https://www.infineon.com/cms/en/product/promopages/aurix-development-studio/

软件使用说明：https://mp.weixin.qq.com/s/elPue25tVmXWw32yJZbUDA

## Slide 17

2

工程目录结构


- CODE文件夹下放置的是逐飞科技精心编写的无刷电机驱动相关代码。
- Infineon_libraries是英飞凌官方的底层驱动，如果还需要其他的单片机片内外设功能，可以基于Infineon_libraries自行编写程序实现。
- Seekfree_libraries和seekfree_peripheral则是逐飞基于TC264制作的应用底层库。
- user文件夹下放置的是主程序及中断文件。

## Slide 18

3

资源使用讲解

内外设以及驱动代码：


- ADC：主要用于检测电源电压、采集放大时候的母线电流以及相电流
- Ccu6定时器：主要用于输出电机所需要用到的互补PWM信号，并且实现自动堵转保护，无需代码干预，当母线电流超过设定值的时候，自动关闭定时器输出。
- GPIO：主要用于LED指示灯，用于显示各种状态，并且初始化输出方向信息和速度信息的端口。
- 按键：通过板载的按键来改变输入来源，可在板载电位器和用户PWM信号之间切换。
- PWM输入：使用GTM模块的输入捕获实现对外部PWM信号的周期以及占空比获取。

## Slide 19

4

程序运行流程


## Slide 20

5

实际效果演示

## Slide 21

让创造变得简单
Make creation easy

逐飞科技微信公众号

17届平衡单车组QQ交流群

Thanks！

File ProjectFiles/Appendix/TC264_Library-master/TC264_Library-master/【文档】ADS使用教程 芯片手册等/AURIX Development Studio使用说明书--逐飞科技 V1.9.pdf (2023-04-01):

2021

# AURIX Development Studio 环境使用说明

# SEEKFREE


AURIX Development Studio 环境使用说明 | 逐飞科技
目录

# SEEKFREE

# SEEKFREE

# 1.使用 AURIX Development Studio 导入工程

安装完成 AURIX Development Studio（在后面的描述中简称为 ADS）后并打开，安装

的时候请务必保证 ADS 安装路径没有中文与空格，只允许使用英文、数字与下划线！初次打

开需要选定工作空间路径，请注意工作空间路径不要包含中文以及空格，只允许使用英文、数

字与下划线！

本章节介绍如何使用 ADS 导入现有工程。本文仅作为参考，仅针对 TC264 芯片，以及逐

飞科技 TC264 开源库。请严格按照手册执行，避免出现额外的问题。

## 1.1.导入工程

单击 ADS 的菜单栏 File 选项，单击 Import...选项，打开导入选项卡。或者在工作空间选

项卡区域单击鼠标右键，找到 Import...选项，打开导入选项卡。

在导入选项卡中打开 General 下拉选项，选择 Existing Project into Workspace 选项，

单击 Next 进入下一步。

# SEEKFREE


这里简单的对导入工程的界面进行说明：

1. 选择工程路径，单击 Browse 按钮可以弹出文件选择窗口，可以找到自己的工程再确

定添加。

2. 直接输入工程路径，相对于 Browse 选择会更快，一般的操作是在文件夹直接复制工

程路径，然后粘贴到此处即可。

3. 选择需要添加的工程，ADS 会扫描选择路径下的所有工程文件，如果只有一个就默认

勾选，如果有多个可以由用户自行选择。

4. 是否复制到工作空间，如果 ADS 版本号低于 1.5.2，那么我们建议勾选复制到工作空

间，否则会出现一些意料之外的 bug。如果版本号高于 1.5.2，就可以由用户自行决定

了，复制到工作空间可以增加代码的安全性，不复制可以节约添加工程的时间。

5. 选择完成后点击 Finish 即可完成添加。


注意：如果 ADS 当前工作空间存在同名工程，那么将无法添加。如果 ADS 工作空间路径内

存在同名工程，那么将无法复制工程到工作空间。

# SEEKFREE

## 1.2.编译工程并进行调试

初次导入工程会发现部分操作按钮是灰色的，这里我们还需要一个步骤，鼠标右击目标工

程，然后选择“Set Active Project”，单击后会发现工程名称加粗，并且上面的按钮也亮起来

SEEKFREE

了。

右键工程并且单击 Clean Project 清理工程！

此时再对工程进行编译操作，推荐右键工程单击 Build Project。


在进行调试工程前请务必确认已经正确连接调试下载器！并且连接好了核心板！

在进行调试工程前请务必确认已经正确连接调试下载器！并且连接好了核心板！

在进行调试工程前请务必确认已经正确连接调试下载器！并且连接好了核心板！

工程编译完成且无报错后，找到上方瓢虫图案旁边的小三角，点击会弹出选择窗口，选择

进入 Debug Configuration 选项卡。

在 Debug Configuration 选项卡中，如果 TASKING C/C++ Debugger 下没有 debug

项目，那么就需要单击新建 launch，然后选中新建的 launch 进行设置。这里如果已经有可选

的 launch，那么只需要确认选项即可。

将 Configuration 选项设置为 TC26xB（这里导入的是我们 TC264 的开源库所以这里设

置为 TC26xB）。然后单击 Debug 进行调试。


完成初次调试后，再次调试就不会进行调试的编译过程(工程未作修改的情况下)，直接进

入调试界面。推荐使用我们提供的说明中的调试步骤进行调试。

至此导入以及编译调试整个流程完成。

# SEEKFREE

# 2.编译、调试与下载

## 2.1.编译工程

SEEKFREE

编译工程步骤与其他环境差别不大，方式为：

1. 通过右键工程选择 Build Project 选项；
2. 上方选项栏中 Build 或 Rebuild 选项 ；

下方 Console 选项卡会输出编译步骤以及最终耗时，Problems 会输出错误以及警告信

息。

## 2.2.仅下载程序

1.8.0 版本的 ADS 有仅下载程序到 Flash 的功能，可点击工具栏的 Flash current project

按键下载当前的工程到单片机。

## 2.3.调试工程

在进行调试工程前请务必确认已经正确连接调试下载器！并且连接好了核心板！

在进行调试工程前请务必确认已经正确连接调试下载器！并且连接好了核心板！

在进行调试工程前请务必确认已经正确连接调试下载器！并且连接好了核心板！

工程编译完成且无报错后，找到上方瓢虫图案旁边的小三角，点击会弹出选择窗口，或者

右键工程选择 Debug As 进入 Debug Configuration 窗口进进入调试。

SEEKFREE

在 Debug Configuration 选项卡中，如果 TASKING C/C++ Debugger 下没有 debug

项目，那么就需要单击新建 launch，然后选中新建的 launch 进行设置。这里如果已经有可选

的 launch，那么只需要确认选项即可。将 Configuration 选项设置为 TC26xB（这里导入的

是我们 TC264 的开源库所以这里设置为 TC26xB）。然后单击 Debug 进行调试。

报这个错证明没有检测到调试下载器、没有检测到芯片（核心板）。请检查调试下载器是

否正确连接，核心板硬件连接是否正确。调试下载器是否正常被电脑识别，DAS Device

Scanner 是否能够扫描到核心。详见 5.1 硬件未连接报错。

## 2.4.单步调试与断点功能

设置断点可以通过在需要设置断点的行数左侧双击设置断点。

右键该位置可以进行断点的相关操作，例如取消、启用、屏蔽等。


进入 Debug 模式后，点击工具栏 Resume<快捷键 F8>选项即可运行代码，运行到

断点处即停止，此刻可以使用 Step Into<快捷键 F5>进行指令单步<每个操作为一步，可

以跳转到所调用函数的定义>调试，或可以使用 Step Over<快捷键 F6>进行代码单步<当

前函数单行为一步>调试。

可以通过 Terminate <快捷键 CTR+F2>结束调试，结束调试后 TASKING 并不会自

行跳转回到代码编辑界面，请在窗口上方工具栏右侧，单击 TASKING C/C++切换回代码编

辑界面。

## 2.5.变量查看功能

在调试界面内，可以通过上方<默认在上方>的 Expressions 选项卡查看全局变量。单击

“Add new expression”，然后输入想要查看的变量即可。当然，Expressions 并不局限于

查看全局变量，当运行到指定函数时也能查看局部变量，也可以查看结构体或者一个计算式子。

唯一得不足就是无法实时查看，需要暂停运行后才能查看值。

# SEEKFREE


## 2.6.内存查看功能

ADS 同样提供了内存查看的工具，可以直接查看指定地址下的数据情况，在下方<默认下

方>的 Memory 选项卡可以通过 Monitors 功能添加映射地址，在 New Renderings...选项卡

可以添加不同的数据格式，具体操作如下图：

在 New Renderings...选项卡可以针对一个地址添加不同的数据格式，具体操作如下图：


## 2.7.printf 输出功能

从 1.1.6 版本的开源库起，printf 重定向为使用串口输出，不再输出至调试的 FSS 窗口。

开源库版本信息在每个工程的 Libraries->doc 文件夹下的 version.txt 文件中有详细记

录，该文件记录当前工程使用的开源库底层的版本。

在 1.1.6-2.9.9 之内的开源库版本工程中，printf 会通过 get_clk 函数中初始化的 Debug

UART 输出，Debug UART 使用的串口号可以在“TC264_config.h”头文件中看到定义。


在 3.0.0 以上的开源库版本工程中，printf 会通过 debug_init 函数中初始化的 Debug

UART 输出，Debug UART 使用的串口号可以在“zf_common_debug.h”头文件中看到定

义。

# SEEKFREE


在 1.1.6 以下的开源库版本工程中，通过 ADS 本身提供的 log 输出的工具，可以使用

printf 函数将 log 信息输出到在下方<默认下方>的 FSS 选项卡。

为了方便调试，可以在 debug 版本代码中添加 log 输出，相对会更加方便调试，更加友

好，而在 release 版本代码中可以将 log 输出删除以提高运行效率。如果找不到 FSS 窗口或者

不小心将 FFS 串口关闭了，请看下一章节的添加面板的介绍。

## 2.8.新建窗口面板

在调试时可能会需要用到某些窗口，如果之前关闭了或者没有需要的信息窗口，可以通过

新建调试窗口面板添加，这里以 FSS 窗口为例：

# SEEKFREE


单击菜单栏 Window 选项，在 Show View 下拉菜单中选择 Other…选项，选中 FSS 并单

击 Open 即可新建一个 FSS 窗口。

如果需要其他窗口，以同样的方式找到对应的窗口 Open 即可。

# SEEKFREE

# 3.工作空间管理

## 3.1.切换工作空间

如果需要切换工作空间，请务必注意工作空间路径不要包含中文以及空格！

按照上述步骤，即可切换工作空间路径，确认后 ADS 会重新启动一次并切换到新的工作

空间路径。

请不要随意改动当前工作空间路径以及路径中的文件夹名称！如果当前工作空间路径包含

中文，也不要直接对工作空间路径中中文部分进行直接修改，请按照上述步骤更改工作空间路

径！

## 3.2.切换工程

当你的工作空间中留存有许多的工程时，需要注意打开的源文件是否是 Active Debug

状态，Active Debug 状态下的工程会在 C/C++ Projects 选项卡中以粗体标示，表示当前该

工程处于 Active Debug 状态，编译、调试等操作会针对于该工程进行。


如左图所示，我当前打开了例程<3-PIT_Demo>的源文件，但实际 Active Project 为<2-

LED_Blink_Demo >，所以此时我点击编译时，会编译例程<2-LED_Blink_Demo >而不是<3-

PIT_Demo >，请务必注意这一点。此时，我们需要切换<3-PIT_Demo >为 Active Debug

状态，在需要调试的工程上右键选择 Set Active Project，如友图所示。

切换后，3-PIT_Demo >变为 Active Debug 状态，此时再进行编译、调试等操作时，就

会以<3-PIT_Demo >工程为基础进行。

## 3.3.打开或关闭工程

工程处于打开状态时，图标显示为带折叠箭头的打开的文件夹，工程处于关闭状态时，图

标显示为不带折叠箭头的关闭的文件夹。

工作空间内工程处于打开状态时，使用 Build ALL 操作时会对所有打开工程进行编译操

# SEEKFREE

作，请务必注意。

关闭工程的操作为：右键工程->Close Project。打开工程的操作为：双击工程。

## 3.4.删除工程


如果当前工作空间内有工程不需要进行修改、调试时，可以将其移除工程，操作为：右键

工程->Delete。此时会弹出 Delete Resources 窗口。

如果勾选 Delete project contents on disk(cannot be undone)选项会从工作空间中

移除该工程并且从磁盘<硬盘>中彻底删除该工程，请谨慎操作！


如果不勾选该选项，则只从工作空间删除该工程，可以在需要该工程时通过 Import 从工

作空间所在目录添加该工程回到工作空间<参考 1.1>。

# SEEKFREE

## 3.5.重命名工程

我们选中需要重命名的工程，右键，选中 Rename…选项。

虽然使用此方法可以重命名工程，但我们并不建议如此使用，因为 ADS 目前版本还存在

重命名的 bug——仅会修改.project 文件内的工程名字，而不修改.cproject 文件。这将导致

用户无法正常进行 debug 调试。我们的建议是手动修改工程名字：

1.修改工程文件夹名字。

2.使用记事本打开.project 文件，使用 Ctrl+H 替换掉原来的工程名。

3. 使用记事本打开.cproject 文件，使用 Ctrl+H 替换掉原来的工程名。

## 3.6.添加、新建文件

如果需要向工程中添加文件，需要注意包含路径的问题，我们的开源库本身的包含路径已

经设置完善，并且我们推荐各位在我们开源库下的 CODE 文件夹下新建文件。

### 3.6.1.文件管理器添加文件

首先是通过文件管理器直接添加文件的方式，我们默认各位按照我们之前的导入工程步骤

操作，那么此时的工程对应的实际位置，就在工作空间的文件夹下。

# SEEKFREE

SEEKFREE

那么我们打开文件管理器，找到对应的工作空间路径，打开对应的工程文件夹，进入我们

推荐的添加文件的文件夹 CODE，这里我们以 2-LED_Blink_Demo 工程为例：

然后回到 ADS 中，选中并右键 2-LED_Blink_Demo 工程，单击 Refresh 刷新工程，此时

即可在 CODE 目录下看到新增的文件：

### 3.6.2.ADS 新建文件

然后是直接使用ADS自身的新建功能新建文件，首先选中目录并右键选择New->Other：

然后在弹窗中选择相应的文件类型，单击下一步：

然后输入文件名，单击完成即可，请注意只允许使用英文、数字与下划线：


### 3.6.3.直接添加文件

最后一个是最直接简单粗暴的方法，直接添加文件：

直接将文件拖动到 ADS 中，此时会直接拷贝一份该文件在对应目录下，并添加到工程内。

# SEEKFREE

## 3.7.包含路径


我们的库中已经设置好了相应的包含路径，包含路径查看如下：

如果需要添加自己的文件夹目录，需要在这里设置添加对应的包含路径。

注意：1.5.2 以上版本的 ADS 默认设置为自动包含路径，工程文件夹内的所有文件都会主

动进行包含，无需用户再进行路径添加的操作。

# SEEKFREE

# 4.环境设置

## 4.1.字体设置


ADS 默认的字体是非等宽的字体，这样会导致代码对齐变得困难，并且格式变得混乱，

显得代码格式杂乱，不美观，不方便查找与编写。 SEEKFREE 所以我们需要重新设置字体，使用等宽字体保证代码的美观性与可阅读性。

## 4.2.拼写报错屏蔽设置

在 ADS 中默认对注释也有拼写检查，会在注释里提示拼写错误：

按照下述方法将拼写报错关闭即可。

完成后不再提示拼写错误：

# SEEKFREE

# 5.常见问题及解决方案

## 5.1.硬件未连接报错

报这个错证明没有检测到调试下载器、没有检测到芯片（核心板）。

请检查调试下载器是否正确连接，核心板硬件连接是否正确。调试下载器是否正常被电脑

识别，DAS Device Scanner 是否能够扫描到核心。在开始菜单中找到 DAS Device Scanner。

打开后按照下图所示操作：


如果显示 No device 的话证明没有检测到芯片，请检查连接。

# SEEKFREE

如果显示 TriCore-Family 的话证明检测到芯片，回到 ADS 继续调试，如果依旧报同样错

误则 clean 工程后删除 launch 调试配置重新编译构建，参见 2.3 章节。

## 5.2.宏定义未生效问题

SEEKFREE

修改宏定义后直接编译调试，发现工程异常，程序运行没有按照宏定义正常生效，该问题

是 ADS 本身的问题，需要 Clean 工程后重新编译工程即可。

## 5.3.每次调试时都会重新编译的问题

在导入以往工程，或者别人的工程时，有部分工程设置不会跟随导入改变，会出现一些问

题，其中包括在每次调试时，都会重新编译工程，十分浪费时间。

如果出现该现象，右键工程打开工程设置，查看工程的关联设置：

## 5.4.重命名工程后编译、调试报错的问题

与 5.3 章节一样，如果出现该现象，右键工程打开工程设置，查看工程的关联设置。

# 6.ADS 下载方式

## 6.1.百度云盘下载

在电脑上安装百度云盘的软件后，在浏览器中输入一下链接，页面打开后输入提取码，即

可进入下载页面。链接中包含了 ADS 软件 1.8.0 版本以及使用 ADS 的详细教程。如果 ADS

有更新我们将会在这个链接上进行同步更新。

链接： https://pan.baidu.com/s/1s340z2pADOTttxliqaqwgA

提取码：kscj

## 6.2.官网下载

第一步先打开英飞凌官网并注册账号。

第二步打开这个链接

https://www.infineon.com/cms/en/product/promopages/aurix-development-

studio/#。 (https://www.infineon.com/cms/en/product/promopages/aurix-development-studio/)

第三步点击 Download here，然后填写信息等待官方将下载地址发到注册账号时填写的

邮箱。

第四步收到下载链接后，打开下载链接即可开始下载 ADS。

# SEEKFREE

# 7.文档版本

版本号 | 日期 | 内容变更
V1.0 | 2020-10-09 | 初始版本
V1.1 | 2020-10-12 | 更新 project_file 文件夹，简化步骤
V1.2 | 2020-10-26 | 增加下载说明
V1.3 | 2020-11-02 | 增加切换工作空间描述、增加文件添加 描述、增加调试硬件连接提示
V1.4 | 2020-11-05 | 新增工程重命名，添加拼写报错设置
V1.5 | 2020-11-25 | 新增 Flash 下载描述、开源库版本描述 以及修改排版
V1.6 | 2020-12-01 | 删除导入修改工程部分
V1.7 | 2021-01-12 | 新增常见错误章节 修改文件添加描述
V1.8 | 2021-01-21 | 更新 printf 描述 新增调试窗口添加 添加重命名工程报错问题
V1.9 | 2022-12-07 | 简化部分操作步骤

# SEEKFREE

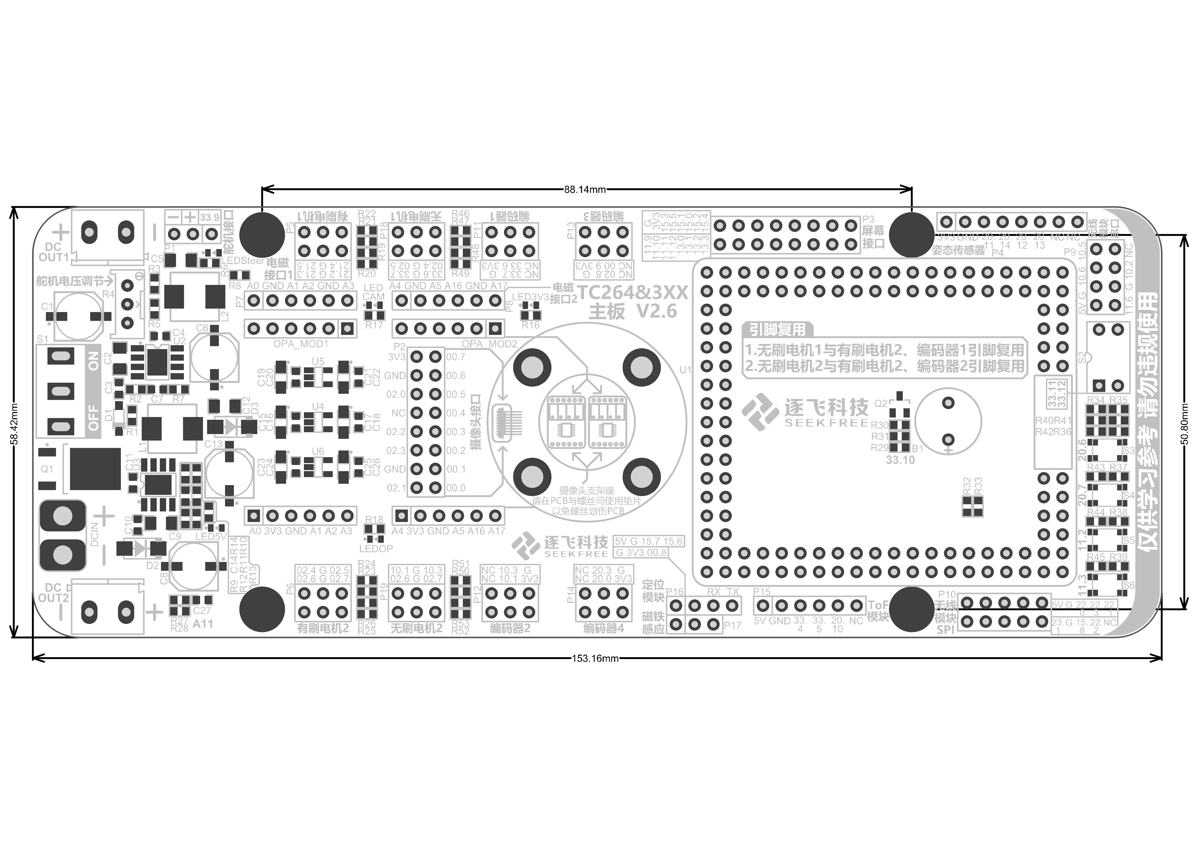
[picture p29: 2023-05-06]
ProjectFiles/Appendix/主板/【原理图】主板原理图、丝印图、位号图/TC264_主板_尺寸图_V2.6.png

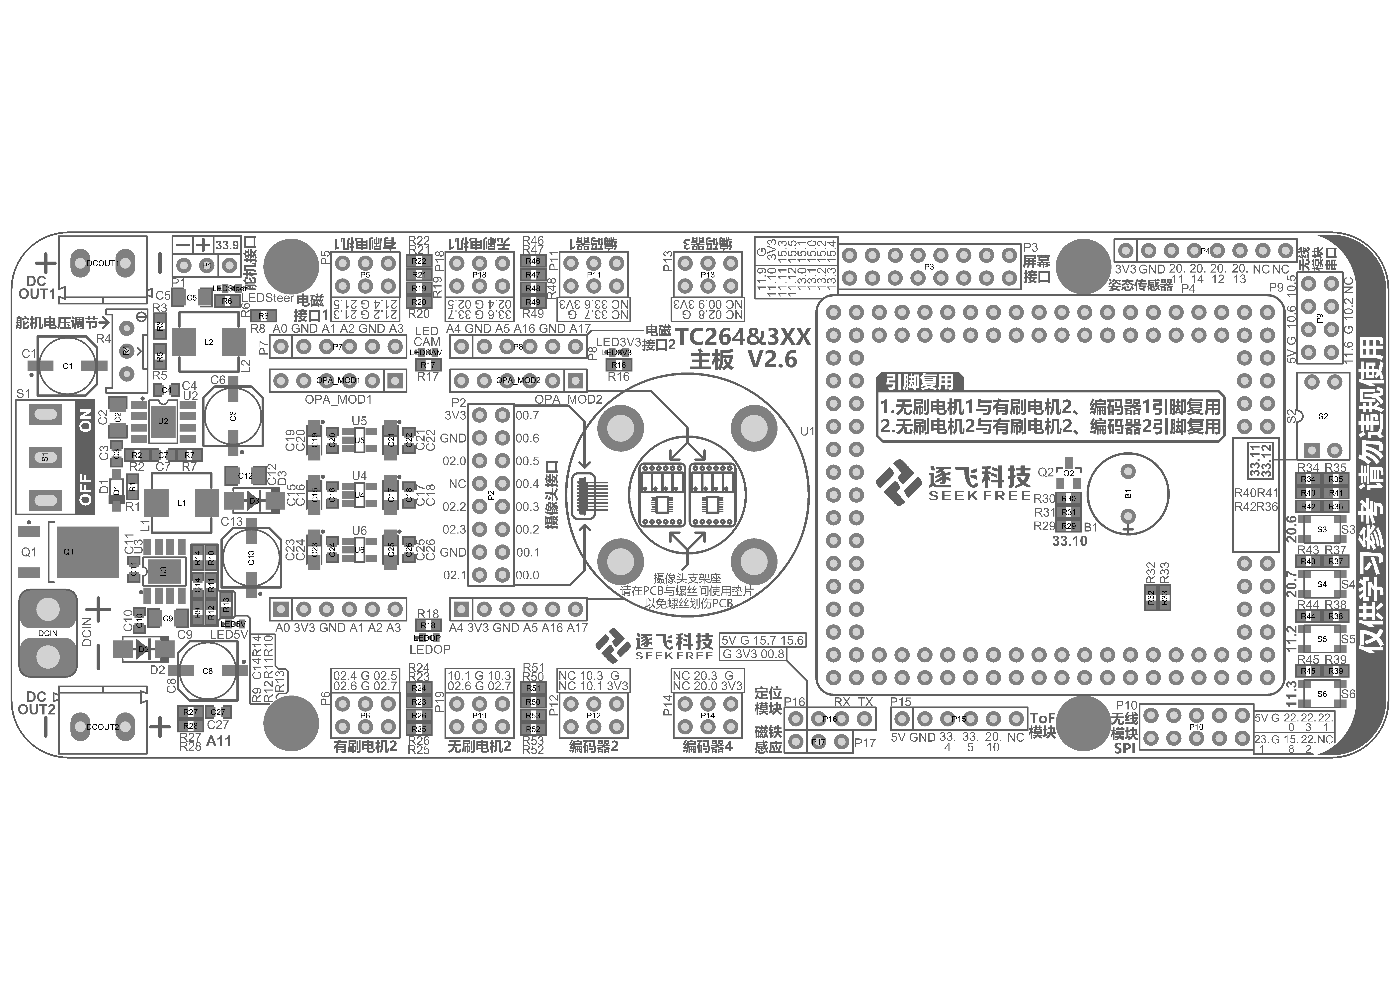
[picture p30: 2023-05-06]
ProjectFiles/Appendix/主板/【原理图】主板原理图、丝印图、位号图/TC264_主板_位号图 正面_V2.6.png

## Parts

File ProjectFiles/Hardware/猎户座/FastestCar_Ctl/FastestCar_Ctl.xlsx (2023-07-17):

Comment | Description | Designator | Footprint | Quantity | Value
100uF 35V 铝电解 | 贴片电解电容 100uF 35V 6.3x7.7 | 32, C6, C9 | CAP-E-S 6.3 | 3 | 100uF
4.7uF 35V X5R | 贴片瓷片电容; MLCC; 1206(3216); | 33, C4, C10 | CAPC3216[1206]S | 3 | 4.7uF
BEEP | 蜂鸣器 | B1 | BEEP 9x5.5mm | 1
100nF 50V X7R | 贴片瓷片电容; MLCC; 0603(1608); | C1, C5, C8, C11, C16, C18, C34, C35, C38 | CAPC1608[0603]S-N | 9 | 100nF
220uF 25V 铝电解 | 贴片电解电容 220uF 25V 6.3x7.7 | C2, C13, C37 | CAP-E-S 6.3 | 3 | 220uF
47uF 25V X5R | 贴片瓷片电容; MLCC; 1206(3216); | C3, C12, C36 | CAPC3216[1206]S | 3 | 47uF
4.7nF 50V X7R | 贴片瓷片电容; MLCC; 0603(1608); | C7, C14 | CAPC1608[0603]S-N | 2 | 4.7nF
10uF 16V 钽电容 | 贴片钽电容 10uF 3216 16V | C15, C17 | CAP-T-S 3216 | 2 | 10uF
22uF 25V X5R | 贴片瓷片电容; MLCC; 0805(2012); | C19, C23 | CAPC2012[0805]S-N | 2 | 22uF
100nF 16V X7R | 贴片瓷片电容; MLCC; 0402(1005); | C20, C22, C24 | CAPC1005[0402]S-N | 3 | 100nF
220pF 50V X7R | 贴片瓷片电容; MLCC; 0402(1005); | C21 | CAPC1005[0402]S-N | 1 | 220pF
10nF 50V X7R | 贴片瓷片电容; MLCC; 0402(1005); | C25, C26, C27, C28 | CAPC1005[0402]S-N | 4 | 10nF
470uF 35V 聚合物固态 | 直插固态电容 470uF 35V 8x14 | C29, C30, C31 | Cap-S-D 3.5-8x14 | 3 | 470uF
4.7nF 50V X7R | 贴片瓷片电容; MLCC; 0402(1005); | C39 | CAPC1005[0402]S-N | 1 | 4.7nF
Header 3 | Header, 6-Pin | Ctl | ZH1.5-6P-SH | 1
BZT52C16 | 稳压二极管 齐纳二极管 Zener Diode | D1 | SOD-123-L | 1
SMDJ26CA | TRANSIENT VOLTAGE SUPPRESSOR DIODE | D2, D3, D4 | SMC[DO-214AB]-Bi | 3
SS54 | SS54 肖特基二极管 | D5, D6 | SMA-L[DO-214AC] | 2 | SS54
Header 2 | Header, 6-Pin | FeedBack | ZH1.5-6P-SH | 1
Header 1 | Header, 6-Pin | Hall | ZH1.5-6P-SH | 1
翠绿贴片LED | 翠绿贴片LED | HALL-5V, LED3V3, LED5V, LEDSreer | LEDC1608(0603)-L | 4
4.7uH 5A | 功率电感 | L1, L2 | 0630 TPC 7*7*3 | 2 | 4.7uH
4.7uH 2A | 功率电感 | L3 | SLO2520 | 1 | 4.7uH
4.7uH 5A | 功率电感 | L4 | SLO2520 | 1 | 4.7uH
屏幕 | 2x8pin, 直插, 双排座 | P1 | HDR2X8-F | 1 | 屏幕
GPS | 1x4pin, 直插, 排针 | P2 | HDR1X4-M | 1 | GPS
IMU | 1x8pin, 直插, 排针 | P3 | HDR1X8-M | 1 | IMU
Header-D-F 2x4P | 2x4pin, 直插, 双排座 | P4 | HDR2X4-F | 1 | Header-D-F 2x4P
Header-D-M 1x3P | 1x3pin, 直插, 排针 | P5 | HDR1X3-M | 1 | Header-D-M 1x3P
HY19P03 | HY19P03 P-Channel MOSFET | Q1 | TO-252AA | 1
S8050 | NPN 三极管 | Q2 | SOT-23 | 1
10K ±1% | 贴片电阻 | R1, R7, R13 | RESC1608[0603]S-N | 3 | 10K
27K ±1% | 贴片电阻 | R2 | RESC1608[0603]S-N | 1 | 27K
3362P-1-503 |  | R3 | RES-ADJ-TH_3P-L7.1-W6.9-P2.50-L_3362P | 1
200K ±1% | 贴片电阻 | R4, R11 | RESC1608[0603]S-N | 2 | 200K
8.2K ±1% | 贴片电阻 | R5 | RESC1608[0603]S-N | 1 | 8.2K
20K ±1% | 贴片电阻 | R6, R8 | RESC1608[0603]S-N | 2 | 20K
51K ±1% | 贴片电阻 | R9 | RESC1608[0603]S-N | 1 | 51K
4.7K ±1% | 贴片电阻 | R10, R16, R18, R19, R20, R21, R22, R23, R45 | RESC1608[0603]S-N | 9 | 4.7K
1.5K ±1% | 贴片电阻 | R12 | RESC1608[0603]S-N | 1 | 1.5K
2.7K ±1% | 贴片电阻 | R14 | RESC1608[0603]S-N | 1 | 2.7K
10R ±1% | 贴片电阻 | R15 | RESC1608[0603]S-N | 1 | 10R
1K ±1% | 贴片电阻 | R17 | RESC1608[0603]S-N | 1 | 1K
470R ±1% | 贴片电阻 | R24, R25, R26, R27, R28, R29 | RESC1608[0603]S-N | 6 | 470R
100R ±1% | 贴片电阻 | R30 | RESC1608[0603]S-N | 1 | 100R
73.2K ±1% | 贴片电阻 | R31 | RESC1005[0402]S-N | 1 | 73.2K
10K ±1% | 贴片电阻 | R32, R43 | RESC1005[0402]S-N | 2 | 10K
100R ±1% | 贴片电阻 | R33, R38, R39, R40 | RESC1005[0402]S-N | 4 | 100R
4.7K ±1% | 贴片电阻 | R34, R35, R36, R37 | RESC1005[0402]S-N | 4 | 4.7K
20K ±1% | 贴片电阻 | R41 | RESC1005[0402]S-N | 1 | 20K
140K ±1% | 贴片电阻 | R42 | RESC1005[0402]S-N | 1 | 140K
200K ±1% | 贴片电阻 | R44 | RESC1005[0402]S-N | 1 | 200K
SW-SPDT | 单刀双掷开关 3脚船型、钮子、拨动开关 SPDT Subminiature Toggle Switch | S1 | SS12D10 | 1
SW DIP-2 | 2位拨码开关 | S2 | Code SW-2-DIP-2.54 | 1
Button | 按键 | S3, S4, S5, S6 | PTS810-3*4-CurvePin | 4
Header 4 | Header, 6-Pin | Status | ZH1.5-6P-SH | 1
TC264_CoreBoard | 逐飞科技TC264核心板 | U1 | TC264_CoreBoard | 1
SP1N28STER | SP1N28STER | U2, U3, U6 | SOP-8E | 3 | SP1N28STER
RT9013-33 | 3.3V 500mA SOT-23-5 LDO | U4 | SOT-23-5 | 1
RY8121 | 18V 2A 1MHz Synchronous Step-Down Regulator | U5 | SOT-23-6 | 1
XT30PW-M |  | XT1, XT2 | XT30PW-M | 2

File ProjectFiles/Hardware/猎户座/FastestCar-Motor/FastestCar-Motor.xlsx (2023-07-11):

Comment | Description | Designator | Footprint | Quantity | Value
翠绿贴片LED | 翠绿贴片LED | 3V3, 12V, RUN | LEDC1608(0603)-L | 3
100uF 35V 铝电解 | 贴片电解电容 100uF 35V 6.3x7.7 | C1 | CAP-E-S 6.3 | 1 | 100uF
4.7uF 35V X5R | 贴片瓷片电容; MLCC; 1206(3216); | C2 | CAPC3216[1206]S | 1 | 4.7uF
100nF 50V X7R | 贴片瓷片电容; MLCC; 0603(1608); | C3, C5, C8 | CAPC1608[0603]S-N | 3 | 100nF
4.7nF 50V X7R | 贴片瓷片电容; MLCC; 0402(1005); | C4 | CAPC1005[0402]S-N | 1 | 4.7nF
47uF 25V X5R | 贴片瓷片电容; MLCC; 1206(3216); | C6 | CAPC3216[1206]S | 1 | 47uF
220uF 25V 铝电解 | 贴片电解电容 220uF 25V 6.3x7.7 | C7 | CAP-E-S 6.3 | 1 | 220uF
22uF 25V X5R | 贴片瓷片电容; MLCC; 0805(2012); | C15, C19, C41, C43, C45 | CAPC2012[0805]S-N | 5 | 22uF
100nF 16V X7R | 贴片瓷片电容; MLCC; 0402(1005); | C16, C18, C20, C21, C26, C27, C28, C29, C30, C31, C33, C34, C35, C36 | CAPC1005[0402]S-N | 14 | 100nF
220pF 50V X7R | 贴片瓷片电容; MLCC; 0402(1005); | C17 | CAPC1005[0402]S-N | 1 | 220pF
1uF 16V X5R | 贴片瓷片电容; MLCC; 0402(1005); | C32 | CAPC1005[0402]S-N | 1 | 1uF
10uF 25V X5R | 贴片瓷片电容; MLCC; 0805(2012); | C40, C42, C44 | CAPC2012[0805]S-N | 3 | 10uF
XT30U-M |  | CN1 | CONN-TH_XT30U-M | 1
Header 3 | Header, 6-Pin | Ctl | ZH1.5-6P-SH | 1
SS54 | SS54 肖特基二极管 | D1 | SMA-L[DO-214AC] | 1 | SS54
1N5819HW | 1N5819HW 肖特基二极管 | D2, D6, D7, D8 | SOD-123-L | 4 | 1N5819HW
蓝色贴片LED | 蓝色贴片LED | EN | LEDC1608(0603)-L | 1
SW-SPDT | 单刀双掷开关 3脚船型、钮子、拨动开关 SPDT Subminiature Toggle Switch | ENABLE | SS12D10 | 1
黄色贴片LED | 黄色贴片LED | ERR | LEDC1608(0603)-L | 1
Header 2 | Header, 6-Pin | FeedBack | ZH1.5-6P-SH | 1
4.7uH 5A | 功率电感 | L1 | SLO2520 | 1 | 4.7uH
4.7uH 2A | 功率电感 | L3 | SLO2520 | 1 | 4.7uH
KF/WJ/DG 30x connecter | 接线端子 3Pin | P2 | KF/WJ/DG 301-3p-5.0mm | 1
BSC014N04LS | 英飞凌 N沟 MOS | Q1, Q2, Q3, Q4, Q5, Q6, Q7, Q8, Q9, Q10, Q11, Q12 | TDSON-8 | 12
200K ±1% | 贴片电阻 | R1 | RESC1005[0402]S-N | 1 | 200K
20K ±1% | 贴片电阻 | R2, R53 | RESC1005[0402]S-N | 2 | 20K
140K ±1% | 贴片电阻 | R3 | RESC1005[0402]S-N | 1 | 140K
10K ±1% | 贴片电阻 | R4, R8, R9, R38, R45, R46, R47, R51, R60, R62, R64, R66, R68, R70, R72, R74, R76, R78, R80, R82 | RESC1005[0402]S-N | 20 | 10K
45.3K ±1% | 贴片电阻 | R7 | RESC1005[0402]S-N | 1 | 45.3K
100K ±1% | 贴片电阻 | R10 | RESC1005[0402]S-N | 1 | 100K
100R ±1% | 贴片电阻 | R11, R48, R52, R59, R61, R63, R65, R67, R69 | RESC1005[0402]S-N | 9 | 100R
150K ±1% | 贴片电阻 | R20, R25, R26, R29, R34, R37, R39, R42 | RESC1005[0402]S-N | 8 | 150K
1K ±1% | 贴片电阻 | R21, R22, R23, R24, R27, R28, R30, R31, R32, R33, R35, R36, R40, R41, R43, R44, R55, R56, R57, R58 | RESC1005[0402]S-N | 20 | 1K
15K ±1% | 贴片电阻 | R49 | RESC1005[0402]S-N | 1 | 15K
51K ±1% | 贴片电阻 | R50 | RESC1005[0402]S-N | 1 | 51K
4.7R ±1% | 贴片电阻 | R71, R73, R75, R77, R79, R81 | RESC1608[0603]S-N | 6 | 4.7R
2mR ±1% | 贴片电阻 | R83, R84, R85, R86 | RESC6332[2512]S | 4 | 2mR
Header 4 | Header, 6-Pin | Status | ZH1.5-6P-SH | 1
SP1N28STER | SP1N28STER | U1 | SOP-8E | 1 | SP1N28STER
RY8121 | 18V 2A 1MHz Synchronous Step-Down Regulator | U3 | SOT-23-6 | 1
COS8552SR | COS8552SR 二路通用运算放大器 | U4, U5, U6 | SOP-8 | 3
AUIRS2181 | AUIRS2181 | U7, U8, U9 | SOP-8 | 3

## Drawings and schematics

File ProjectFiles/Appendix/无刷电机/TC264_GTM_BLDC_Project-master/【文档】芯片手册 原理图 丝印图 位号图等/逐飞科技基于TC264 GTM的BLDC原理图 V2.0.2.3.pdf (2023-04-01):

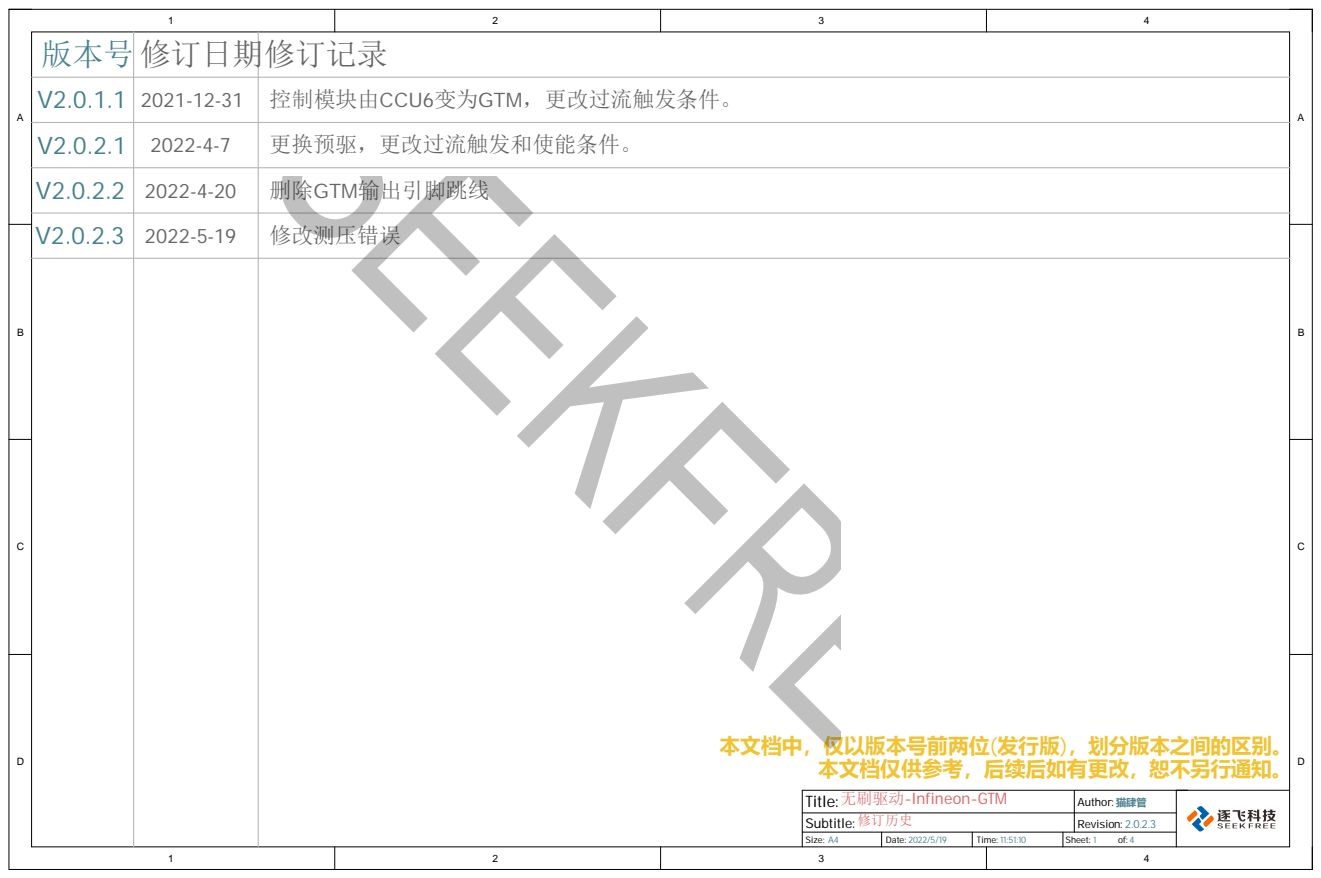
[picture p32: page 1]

本文档中，仅以版本号前两位(发行版)，划分版本之间的区别。

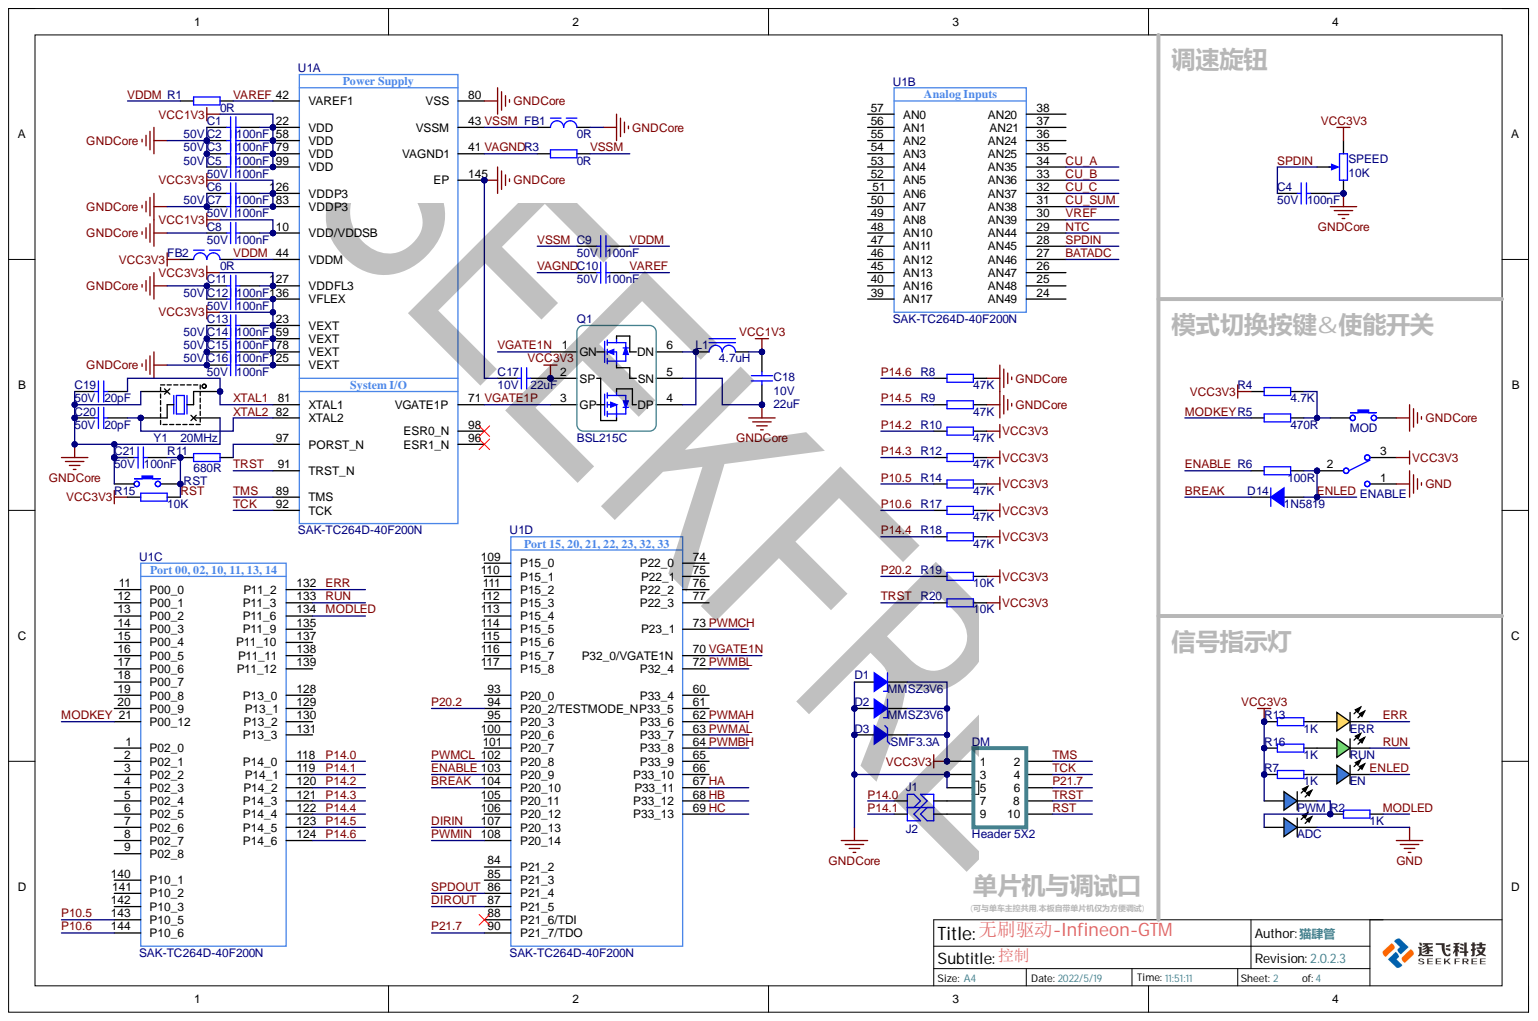
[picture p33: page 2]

C2 | | | VDD 58
50V | C3 | 100nF | | VDD 79
C5 | 100nF | | | VDD 99

VDDP3 126

50V | C7 | 100nF | VDDP3 83

VDDFL3 127

50V | C12 | 100nF | VFLEX 136

50V 50V 50V | C14 | 100nF | VEXT 59
C15 | 100nF | VEXT 78
C16 | 100nF | VEXT 125

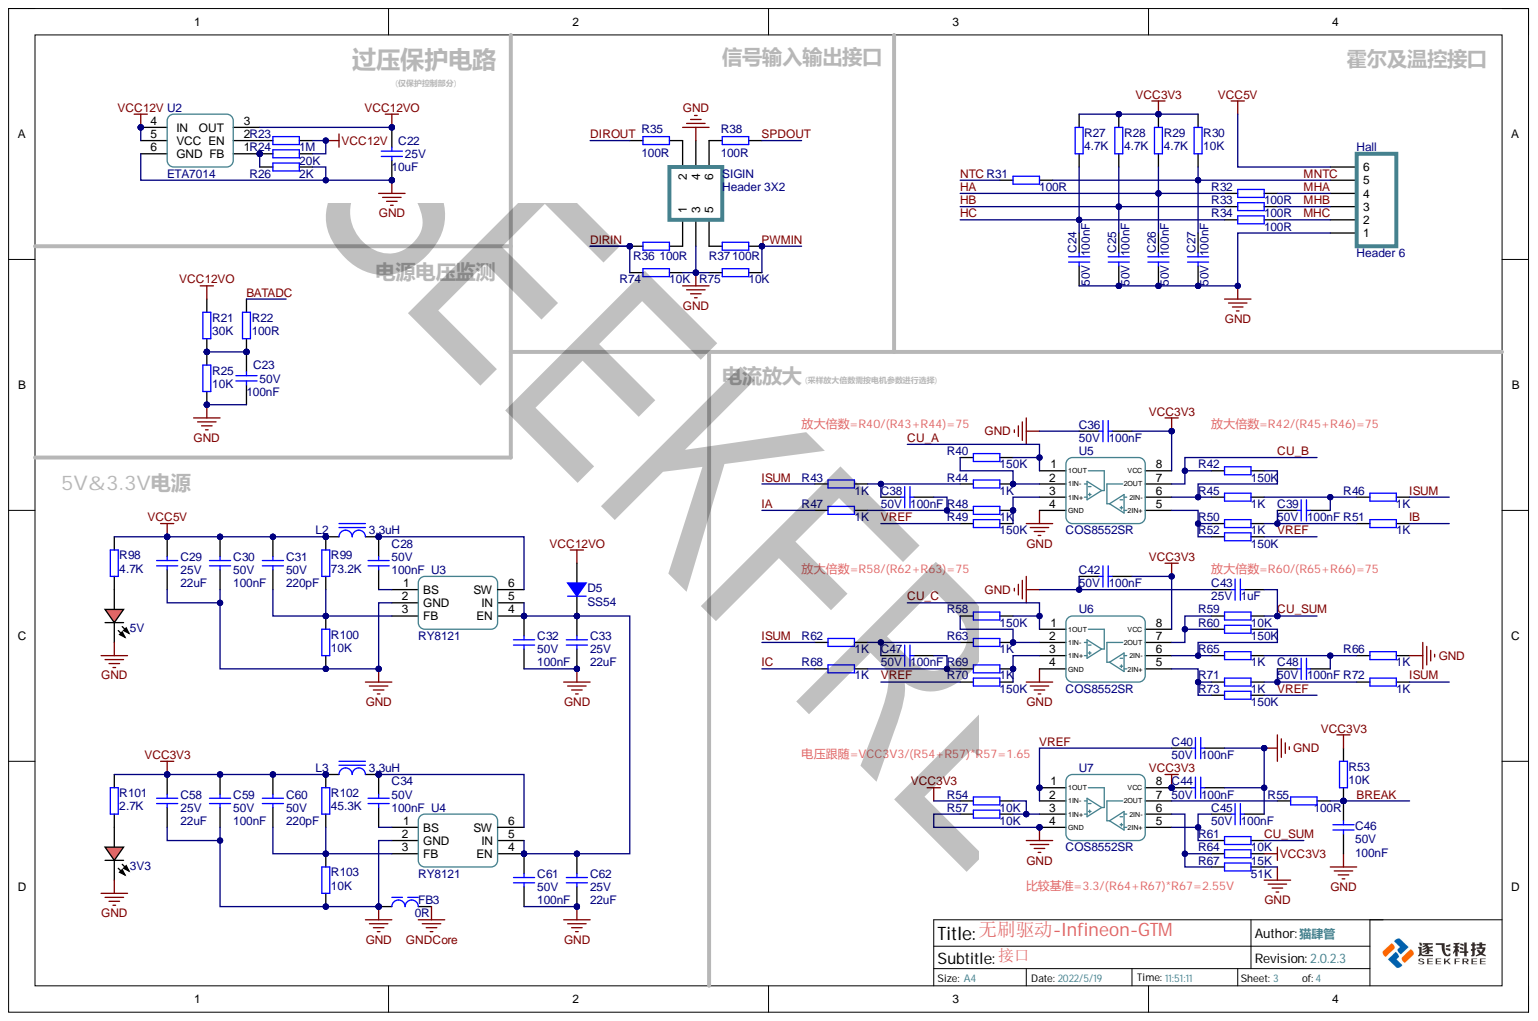
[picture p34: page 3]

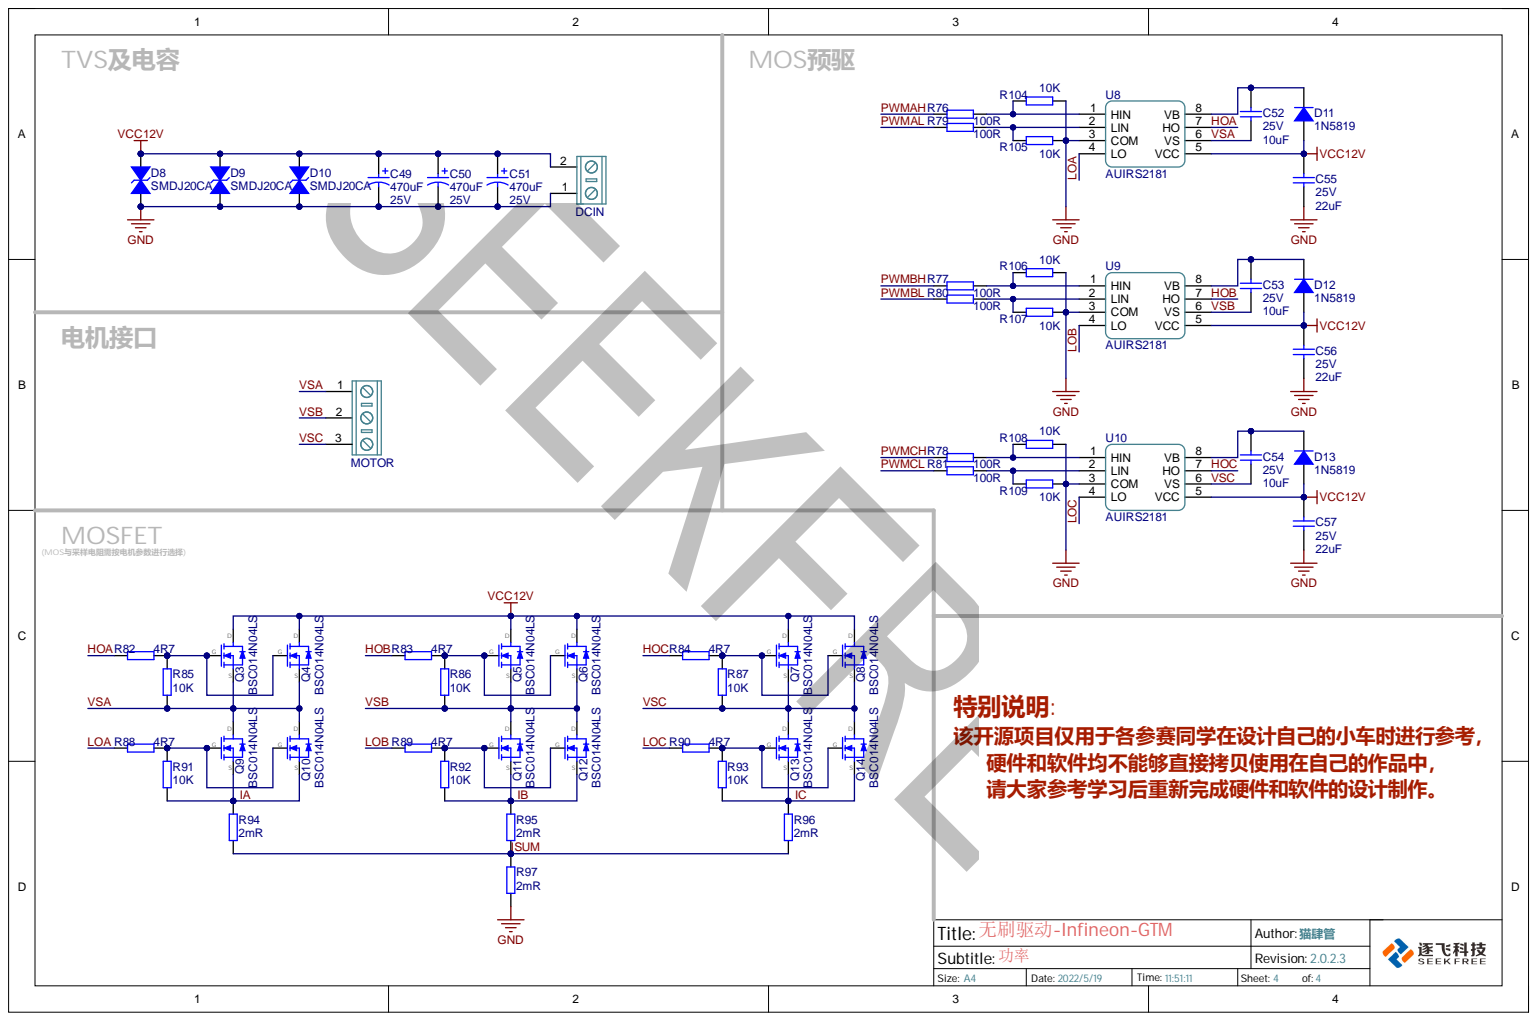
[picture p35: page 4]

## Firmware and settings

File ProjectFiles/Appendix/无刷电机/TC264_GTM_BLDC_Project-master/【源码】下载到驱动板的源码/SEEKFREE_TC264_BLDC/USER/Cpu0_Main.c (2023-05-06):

/*********************************************************************************************************************
 * COPYRIGHT NOTICE
 * Copyright (c) 2020,逐飞科技
 * All rights reserved.
 * 技术讨论QQ群：三群：824575535
 *
 * 以下所有内容版权均属逐飞科技所有，未经允许不得用于商业用途，
 * 欢迎各位使用并传播本程序，修改内容时必须保留逐飞科技的版权声明。
 *
 * @file            main
 * @company         成都逐飞科技有限公司
 * @author          逐飞科技(QQ3184284598)
 * @version         查看doc内version文件 版本说明
 * @Software        ADS v1.2.2
 * @Target core     TC264D
 * @Taobao          https://seekfree.taobao.com/
 * @date            2020-3-23
 ********************************************************************************************************************/


//BLDC

#include "gpio.h"
#include "adc.h"
#include "hall.h"
#include "move_filter.h"
#include "key.h"
#include "motor.h"
#include "pid.h"
#include "headfile.h"
#include "ccu6_pwm.h"
#include "pwm_input.h"
#pragma section all "cpu0_dsram"
//将本语句与#pragma section all restore语句之间的全局变量都放在CPU0的RAM中


//特别说明：该开源项目仅用于各参赛同学在设计自己的小车时进行参考，硬件和软件都不能够直接拷贝使用在自己的作品中，请大家参考后重新完成硬件和软件的设计制作。
//特别说明：该开源项目仅用于各参赛同学在设计自己的小车时进行参考，硬件和软件都不能够直接拷贝使用在自己的作品中，请大家参考后重新完成硬件和软件的设计制作。
//特别说明：该开源项目仅用于各参赛同学在设计自己的小车时进行参考，硬件和软件都不能够直接拷贝使用在自己的作品中，请大家参考后重新完成硬件和软件的设计制作。

int core0_main(void)
{
    //获取时钟频率  务必保留
    get_clk();

    //初始化LED引脚
    led_init();

    //初始化按键引脚
    key_init();

    //初始化adc通道，adc用于采集电源电压、母线电流、相电流的
    adc_collection_init();

    //霍尔初始化
    hall_init();

    //滑动平均滤波初始化
    move_filter_init(&speed_filter);

    //初始化输出速度与方向信息的引脚
    motor_information_out_init();

    //输入信号捕获初始化
    pwm_input_init();

    //电机初始化
    motor_init();

    //PID参数初始化
    closed_loop_pi_init();

    //初始化定时器,用于输出互补PWM
    ccu6_pwm_init();

    //初始化定时器,用于计算占空比
    pit_interrupt_ms(CCU6_0, PIT_CH0, 5);

    enableInterrupts();
    while(1){

        led_output();       //根据当前状态点亮或者熄灭LED灯

        //发送数据到虚拟示波器 虚拟示波器下载链接 https://pan.baidu.com/s/198CMXTZsbI3HAEqNXDngBw
        data_conversion((uint16)speed_filter.data_average, pwm_in_duty, hall_value_now, duty, virtual_scope_data);
        uart_putbuff(UART_0, virtual_scope_data, sizeof(virtual_scope_data));  //数据转换完成后，使用串口发送将数组的内容发送出去
    }
}

#pragma section all restore

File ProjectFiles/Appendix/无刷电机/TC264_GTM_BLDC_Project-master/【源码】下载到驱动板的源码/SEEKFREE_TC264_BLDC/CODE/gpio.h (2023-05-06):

#ifndef _GPIO_H
#define _GPIO_H

#include "common.h"




#define LED_ERR_PIN         P21_2
#define LED_RUN_PIN         P21_3
#define LED_MODEL_PIN       P21_4
#define EN_PIN              P11_6

void led_init(void);
void led_output(void);

#endif

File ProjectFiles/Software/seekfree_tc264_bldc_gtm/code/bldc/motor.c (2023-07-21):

/*********************************************************************************************************************
* TC264 Opensourec Library 即（TC264 开源库）是一个基于官方 SDK 接口的第三方开源库
* Copyright (c) 2022 SEEKFREE 逐飞科技
*
* 本文件是 TC264 开源库的一部分
*
* TC264 开源库 是免费软件
* 您可以根据自由软件基金会发布的 GPL（GNU General Public License，即 GNU通用公共许可证）的条款
* 即 GPL 的第3版（即 GPL3.0）或（您选择的）任何后来的版本，重新发布和/或修改它
*
* 本开源库的发布是希望它能发挥作用，但并未对其作任何的保证
* 甚至没有隐含的适销性或适合特定用途的保证
* 更多细节请参见 GPL
*
* 您应该在收到本开源库的同时收到一份 GPL 的副本
* 如果没有，请参阅<https://www.gnu.org/licenses/>
*
* 额外注明：
* 本开源库使用 GPL3.0 开源许可证协议 以上许可申明为译文版本
* 许可申明英文版在 libraries/doc 文件夹下的 GPL3_permission_statement.txt 文件中
* 许可证副本在 libraries 文件夹下 即该文件夹下的 LICENSE 文件
* 欢迎各位使用并传播本程序 但修改内容时必须保留逐飞科技的版权声明（即本声明）
*
* 文件名称          motor
* 公司名称          成都逐飞科技有限公司
* 版本信息          查看 libraries/doc 文件夹内 version 文件 版本说明
* 开发环境          ADS v1.8.0
* 适用平台          TC264D
* 店铺链接          https://seekfree.taobao.com/
*
* 修改记录
* 日期              作者                备注
* 2023-02-01       pudding             first version
********************************************************************************************************************/

#include <LED.h>
#include "IFXGTM_TIM_IN.h"
#include "ifxGtm_Tim.h"
#include "zf_common_function.h"
#include "zf_driver_delay.h"
#include "zf_driver_timer.h"
#include "bldc_config.h"
#include "move_filter.h"
#include "pwm_input.h"
#include "adc.h"
#include "motor.h"

motor_struct motor_control;

uint32 commutation_time_save = 0;                   // 换相时间

//-------------------------------------------------------------------------------------------------------------------
// 函数简介     电机转速信息输出引脚初始化
// 参数说明     void
// 使用示例     motor_information_out_init();
// 备注信息
//-------------------------------------------------------------------------------------------------------------------
void motor_information_out_init(void)
{
    pwm_init(MOTOR_SPEED_OUT_PIN, 50 , 0);                  // 初始化电机速度输出引脚，输出为频率变化的信号，例如电机转速为每分钟5000转，则引脚上的频率为5000Hz。
    gpio_init(MOTOR_DIR_OUT_PIN , GPO, 0, GPO_PUSH_PULL);   // 初始化电机方向输出引脚（用户端接收）
}

//-------------------------------------------------------------------------------------------------------------------
// 函数简介     切换换相表
// 参数说明     void
// 使用示例     advance_switch();
// 备注信息
//-------------------------------------------------------------------------------------------------------------------
void advance_switch(void)
{
    GTM_SPE0_CTRL_STAT.B.SPE_EN   = FALSE;

    if(motor_control.set_dir == REVERSE)
    {
        GTM_SPE0_OUT_PAT0.U = MOTOR_FOREWARD_0;     // 正转换相表
        GTM_SPE0_OUT_PAT1.U = MOTOR_FOREWARD_1;
        GTM_SPE0_OUT_PAT2.U = MOTOR_FOREWARD_2;
        GTM_SPE0_OUT_PAT3.U = MOTOR_FOREWARD_3;
        GTM_SPE0_OUT_PAT4.U = MOTOR_FOREWARD_4;
        GTM_SPE0_OUT_PAT5.U = MOTOR_FOREWARD_5;
    }
    else
    {
        GTM_SPE0_OUT_PAT0.U = MOTOR_REVERSAL_0;     // 反转换相表
        GTM_SPE0_OUT_PAT1.U = MOTOR_REVERSAL_1;
        GTM_SPE0_OUT_PAT2.U = MOTOR_REVERSAL_2;
        GTM_SPE0_OUT_PAT3.U = MOTOR_REVERSAL_3;
        GTM_SPE0_OUT_PAT4.U = MOTOR_REVERSAL_4;
        GTM_SPE0_OUT_PAT5.U = MOTOR_REVERSAL_5;
    }
    if(motor_control.brake_flag == 1)
    {
        GTM_SPE0_OUT_PAT0.U = MOTOR_BRAKE;          // 刹车
        GTM_SPE0_OUT_PAT1.U = MOTOR_BRAKE;
        GTM_SPE0_OUT_PAT2.U = MOTOR_BRAKE;
        GTM_SPE0_OUT_PAT3.U = MOTOR_BRAKE;
        GTM_SPE0_OUT_PAT4.U = MOTOR_BRAKE;
        GTM_SPE0_OUT_PAT5.U = MOTOR_BRAKE;
    }
    GTM_SPE0_CTRL_STAT.B.SPE_EN   = TRUE;
}

//-------------------------------------------------------------------------------------------------------------------
// 函数简介     设置旋转方向
// 参数说明     void
// 使用示例     motor_set_dir();
// 备注信息
//-------------------------------------------------------------------------------------------------------------------
void motor_set_dir(void)
{
    if(gpio_get_level(MOTOR_DIR_IN_PIN) != motor_control.set_dir)
    {
        motor_control.set_dir = gpio_get_level(MOTOR_DIR_IN_PIN);
        advance_switch();
    }
//    motor_dir_out();
}

//-------------------------------------------------------------------------------------------------------------------
// 函数简介     电机占空比输出
// 参数说明     void
// 使用示例     speed_ctrl();
// 备注信息
//-------------------------------------------------------------------------------------------------------------------
void speed_ctrl(speed_st speed)
{
    // 占空比不能大于周期值
    if( speed.duty <= speed.period )
    {
        GTM_TOM0_CH0_SR1.U = speed.duty     & 0xFFFF;
        GTM_TOM0_CH0_SR0.U = speed.period   & 0xFFFF;
    }
}

//-------------------------------------------------------------------------------------------------------------------
// 函数简介     计算当前的速度
// 参数说明     void
// 使用示例     calc_speed();
// 备注信息
//-------------------------------------------------------------------------------------------------------------------
inline void calc_speed(void)
{
    //转速计算
    int32 speed;

    // 电机转速计算说明
    // 2.commutation_time_save是统计电机单次换相使用了多少时间
    // 3.通常电机转速我们都用RPM表示，RPM表示每分钟电机的转速
    // 3.电机转一圈需要换相的次数等于 电机极对数*6
    // 4.因此电机转速等于 模块时钟/单次换相时间/(电机极对数 * 6) * 60，这样可以得到电机每分钟的转速

    speed = FCY / POLEPAIRS / commutation_time_save * 10;

    // 电机反转的时候需要对速度取反
    if(FORWARD == motor_control.spin_dir)
    {
        move_filter_calc(&speed_filter, speed);
    }
    else
    {
        move_filter_calc(&speed_filter, -speed);
    }


}
//-------------------------------------------------------------------------------------------------------------------
// 函数简介     换相处理 保存在上一相位等待的时间
// 参数说明     void
// 使用示例     phase_change_manage();
// 备注信息
//-------------------------------------------------------------------------------------------------------------------
void phase_change_manage(void)
{
    commutation_time_save = system_getval();
    system_start();

    calc_speed();
}

//-------------------------------------------------------------------------------------------------------------------
// 函数简介     换相超时处理
// 参数说明     void
// 使用示例     phase_change_time_check();
// 备注信息
//-------------------------------------------------------------------------------------------------------------------
void phase_change_time_check(void)
{
    if(system_getval() > (COMMUTATION_TIMEOUT * 1000))
    {
        commutation_time_save = COMMUTATION_TIMEOUT;

        move_filter_init(&speed_filter);                            // 滑动平均滤波初始化
        motor_control.run_state = MOTOR_STOP;
    }
    else
    {
        motor_control.run_state = MOTOR_RUN;
    }
}
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

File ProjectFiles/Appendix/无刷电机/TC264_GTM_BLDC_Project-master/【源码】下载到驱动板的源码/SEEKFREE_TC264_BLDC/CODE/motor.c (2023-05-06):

/*********************************************************************************************************************
 * COPYRIGHT NOTICE
 * Copyright (c) 2021,逐飞科技
 * All rights reserved.
 * 技术讨论QQ群：联系淘宝客服
 *
 * 以下所有内容版权均属逐飞科技所有，未经允许不得用于商业用途，
 * 欢迎各位使用并传播本程序，修改内容时必须保留逐飞科技的版权声明。
 *
 * @file            motor
 * @company         成都逐飞科技有限公司
 * @author          逐飞科技(QQ3184284598)
 * @version         查看doc内version文件 版本说明
 * @Software        ADS v1.5.2
 * @Target core     TC264D
 * @Taobao          https://seekfree.taobao.com/
 * @date            2021-12-10
 ********************************************************************************************************************/

#include "zf_gpio.h"
#include "gpio.h"
#include "hall.h"
#include "pid.h"
#include "bldc_config.h"
#include "IfxCcu6.h"
#include "pwm_input.h"
#include "ccu6_pwm.h"
#include "zf_gtm_pwm.h"
#include "move_filter.h"
#include "SEEKFREE_FUN.h"
#include "motor.h"

int16 duty = 0;           //PWM初值

motor_struct motor_control;

//-------------------------------------------------------------------------------------------------------------------
//  @brief      电机参数初始化
//  @param      void
//  @return     void
//  @since
//-------------------------------------------------------------------------------------------------------------------
void motor_init(void)
{
    #if BLDC_BRAKE_ENABLE==1
        motor_control.brake_flag = 1;   //刹车使能
    #else
        motor_control.brake_flag = 0;   //刹车关闭
    #endif
    motor_control.dir = FORWARD;                    //设置默认的方向
    #if BLDC_CLOSE_LOOP_ENABLE
    motor_control.set_speed = 0;
    motor_control.max_speed = BLDC_MAX_SPEED;       //设置最大正转速度
    motor_control.min_speed = -BLDC_MAX_SPEED;      //设置最大反转速度
    #endif
}

//-------------------------------------------------------------------------------------------------------------------
//  @brief      电机信息输出初始化
//  @param      void
//  @return     void
//  @since
//-------------------------------------------------------------------------------------------------------------------
void motor_information_out_init(void)
{
    gtm_pwm_init(MOTOR_SPEED_OUT_PIN, 50, 0);       //初始化电机速度输出引脚，输出为频率变化的信号，例如电机转速为每分钟5000转，则引脚上的频率为5000Hz。
    gpio_init(MOTOR_DIR_OUT_PIN, GPO, 0, PUSHPULL); //初始化电机方向输出引脚（用户端接收）
}

//-------------------------------------------------------------------------------------------------------------------
//  @brief      开启A相上桥，B相下桥     其他关闭
//  @param      duty    ：  PWM占空比
//  @return     void
//  @since
//-------------------------------------------------------------------------------------------------------------------
void mos_q1q4_open(uint16 duty)
{
    ccu6SFR->MODCTR.B.T12MODEN = 0x0b;

    IfxCcu6_setT12CompareValue(ccu6SFR, IfxCcu6_T12Channel_0, duty);
    IfxCcu6_setT12CompareValue(ccu6SFR, IfxCcu6_T12Channel_1, 0);
    IfxCcu6_enableShadowTransfer(ccu6SFR, TRUE, FALSE);
}
//-------------------------------------------------------------------------------------------------------------------
//  @brief      开启A相上桥，C相下桥     其他关闭
//  @param      duty    ：  PWM占空比
//  @return     void
//  @since
//-------------------------------------------------------------------------------------------------------------------
void mos_q1q6_open(uint16 duty)
{
    ccu6SFR->MODCTR.B.T12MODEN = 0x23;

    IfxCcu6_setT12CompareValue(ccu6SFR, IfxCcu6_T12Channel_0, duty);
    IfxCcu6_setT12CompareValue(ccu6SFR, IfxCcu6_T12Channel_2, 0);
    IfxCcu6_enableShadowTransfer(ccu6SFR, TRUE, FALSE);
}
//-------------------------------------------------------------------------------------------------------------------
//  @brief      开启B相上桥，A相下桥     其他关闭
//  @param      duty    ：  PWM占空比
//  @return     void
//  @since
//-------------------------------------------------------------------------------------------------------------------
void mos_q3q2_open(uint16 duty)
{
    ccu6SFR->MODCTR.B.T12MODEN = 0x0e;

    IfxCcu6_setT12CompareValue(ccu6SFR, IfxCcu6_T12Channel_1, duty);
    IfxCcu6_setT12CompareValue(ccu6SFR, IfxCcu6_T12Channel_0, 0);
    IfxCcu6_enableShadowTransfer(ccu6SFR, TRUE, FALSE);
}
//-------------------------------------------------------------------------------------------------------------------
//  @brief      开启B相上桥，C相下桥     其他关闭
//  @param      duty    ：  PWM占空比
//  @return     void
//  @since
//-------------------------------------------------------------------------------------------------------------------
void mos_q3q6_open(uint16 duty)
{
    ccu6SFR->MODCTR.B.T12MODEN = 0x2c;

    IfxCcu6_setT12CompareValue(ccu6SFR, IfxCcu6_T12Channel_1, duty);
    IfxCcu6_setT12CompareValue(ccu6SFR, IfxCcu6_T12Channel_2, 0);
    IfxCcu6_enableShadowTransfer(ccu6SFR, TRUE, FALSE);
}
//-------------------------------------------------------------------------------------------------------------------
//  @brief      开启C相上桥，A相下桥     其他关闭
//  @param      duty    ：  PWM占空比
//  @return     void
//  @since
//-------------------------------------------------------------------------------------------------------------------
void mos_q5q2_open(uint16 duty)
{
    ccu6SFR->MODCTR.B.T12MODEN = 0x32;

    IfxCcu6_setT12CompareValue(ccu6SFR, IfxCcu6_T12Channel_2, duty);
    IfxCcu6_setT12CompareValue(ccu6SFR, IfxCcu6_T12Channel_0, 0);
    IfxCcu6_enableShadowTransfer(ccu6SFR, TRUE, FALSE);
}
//-------------------------------------------------------------------------------------------------------------------
//  @brief      开启C相上桥，B相下桥     其他关闭
//  @param      duty    ：  PWM占空比
//  @return     void
//  @since
//-------------------------------------------------------------------------------------------------------------------
void mos_q5q4_open(uint16 duty)
{
    ccu6SFR->MODCTR.B.T12MODEN = 0x38;

    IfxCcu6_setT12CompareValue(ccu6SFR, IfxCcu6_T12Channel_2, duty);
    IfxCcu6_setT12CompareValue(ccu6SFR, IfxCcu6_T12Channel_1, 0);
    IfxCcu6_enableShadowTransfer(ccu6SFR, TRUE, FALSE);
}
//-------------------------------------------------------------------------------------------------------------------
//  @brief      关闭所有上桥，开启所有下桥，使电机在线圈的自感电动势的作用下自己完成刹车
//  @param      void
//  @return     void
//  @since
//-------------------------------------------------------------------------------------------------------------------
void mos_close(void)
{
    ccu6SFR->MODCTR.B.T12MODEN = 0x2A;
    IfxCcu6_setT12CompareValue(ccu6SFR, IfxCcu6_T12Channel_0, 0);
    IfxCcu6_setT12CompareValue(ccu6SFR, IfxCcu6_T12Channel_1, 0);
    IfxCcu6_setT12CompareValue(ccu6SFR, IfxCcu6_T12Channel_2, 0);
    IfxCcu6_enableShadowTransfer(ccu6SFR, TRUE, FALSE);
}

void motor_set_dir(void)
{
    //获取方向控制引脚电平并切换对应方向
    if(!gpio_get(MOTOR_DIR_IN_PIN))
    {
        motor_control.dir = FORWARD;
    }
    else
    {
        motor_control.dir = REVERSE;
    }
    //输出电机实际运行的方向信息
    motor_dir_out();
}
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

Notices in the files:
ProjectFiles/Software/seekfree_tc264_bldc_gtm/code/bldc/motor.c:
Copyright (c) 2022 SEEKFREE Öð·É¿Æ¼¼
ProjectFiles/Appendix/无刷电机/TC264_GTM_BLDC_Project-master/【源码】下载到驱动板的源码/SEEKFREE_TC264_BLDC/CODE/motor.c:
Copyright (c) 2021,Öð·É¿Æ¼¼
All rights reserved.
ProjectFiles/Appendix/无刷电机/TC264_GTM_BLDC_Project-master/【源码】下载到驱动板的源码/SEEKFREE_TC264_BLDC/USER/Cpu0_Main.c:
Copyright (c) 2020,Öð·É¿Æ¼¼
